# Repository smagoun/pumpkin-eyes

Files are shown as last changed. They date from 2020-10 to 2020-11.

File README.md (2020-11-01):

# pumpkin-eyes
CircuitPython-powered servo control for animatronic eyeballs, inspired by 68percentwater's [arduino servo pumpkin eyes](https://www.youtube.com/watch?v=ryUNHPJ3leY).

Built for Adafruit [ItsyBitsy Express M0](https://www.adafruit.com/product/3727).

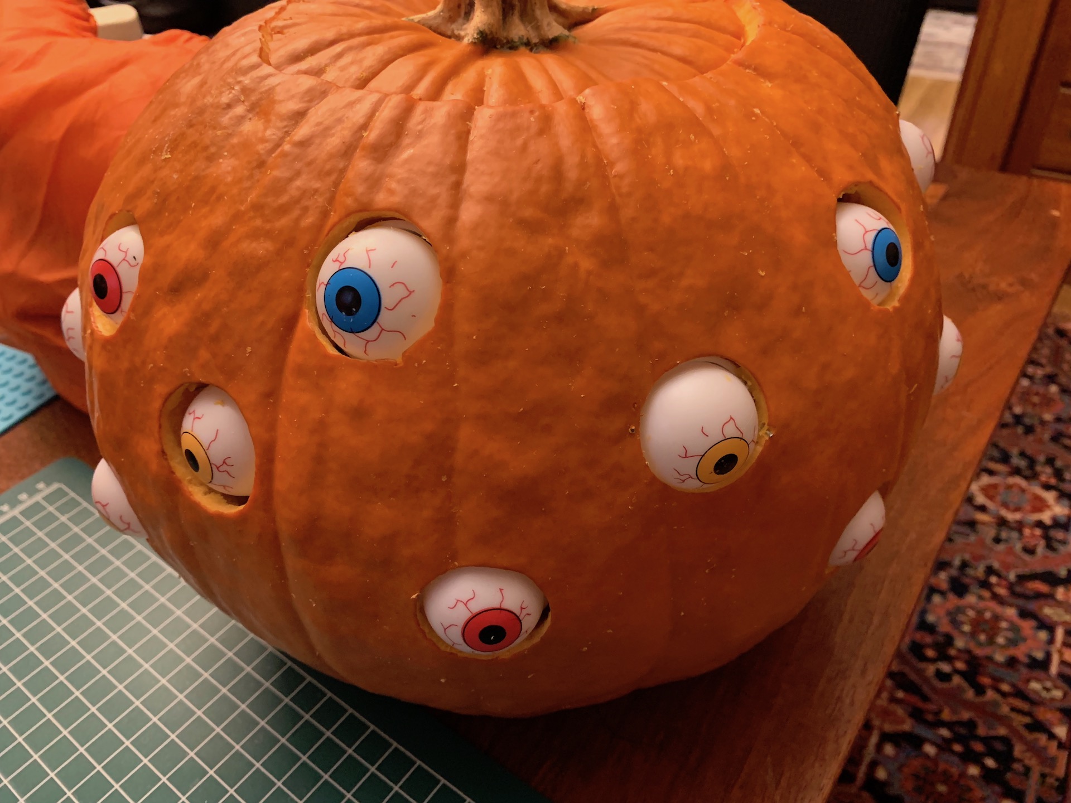
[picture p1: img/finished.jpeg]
Animatronic pumpkin


## Parts list:
* 12x [SG51R Sub-Micro Servos](https://www.adafruit.com/product/2201)
* 1x [ItsyBitsy Express M0](https://www.adafruit.com/product/3727)
* 1x [Half-Size Breadboard](https://www.adafruit.com/product/64)
* 1x [Breadboarding wire bundle](https://www.adafruit.com/product/153)
* 1x [USB Type-A Breakout cable](https://www.adafruit.com/product/4448)
* 1x [NeoPixel Ring - 12x](https://www.adafruit.com/product/1643)
* 1x [Soft tactile button](https://www.adafruit.com/product/3101)
* 2x [1-1/2" sink drain extension tube](https://www.acehardware.com/departments/plumbing/sinks/sink-parts-and-repair/4224051)
* 1x [3-pack of 12 plastic eyeballs](https://www.amazon.com/gp/product/B07582HG6T/ref=ppx_yo_dt_b_asin_title_o03_s00?ie=UTF8&psc=1)
* 1x 5/16" wooden dowel
* Several paper clips, or other stiff wire (baling wire)
* 1x USB battery charger
* 1x large pumpkin (approx 12" diameter)

## Tools:
* Soldering iron
* Wire cutters
* Slip-joint pliers
* Needle-nose pliers
* Hot glue gun
* Fine-tooth razor saw
* File or sandpaper
* Drill with 1/16" and 5/64" bits and 1-3/8" hole saw
* Serrated knife

## Hints + Tips:

### Straightening a paper clip (or baling wire):
1. Pull the paper clip (or wire) mostly-straight by hand
1. If there are bends remaining in the wire, put each bend into the jaws of the pliers and squeeze shut to straighten the bend

### Forming the axles:
1. Straighten a paper clip or other stiff wire and cut a 2" length
1. Use the pliers to bend a short (1/4") 90-degree turn in the wire
1. Feed the other end of the wire through the eyeball (eew!)
1. Bend a 90-degree turn in the other end of the wire, which should now be in a 'U' shape. I found it best to grip the wire with needle-nose pliers just next to the eyeball, then use the slip joint pliers to create the 90-degree bend. Holding the wire with the needle-nose pliers prevents damaging the straight portion of the wire inside the eyeball
1. Use hot glue to affix the bend ends of the wire to the tube. Don't get any glue on the eyeballs!

### Assembling the eyeball mechanism
* Cut the tube into 1" lengths. A little shorter might be better; anything longer will limit the range of motion of the eye.
* The tube I selected happened to fit the eyeballs perfectly. Too perfectly, in fact! Each eyeball has a seam that runs around the middle of the ball. This seam was tall enough to bump into the edge of the tubing. I had to file down the seams on each eyeball to get smooth rotation.
* The eyeballs look better if they have a large range of motion. The range of motion is determined by the relative lengths of the servo horn and the location of the mounting hole in the dowel. To maximize range of motion, mount the control arm close to the base of the dowel. The dowels don't need to be long - 1" is fine.
* For better range of motion, the end of the servo horn should be level with the mounting hole in the dowel. However we also need the mounting hole to be realtively close to the base of the dowel. As a result the servo horn can impact the tube, interfering with range of motion. Cut a notch in the side of the tube to allow the servo horn to traverse freely.
* Use a 5/64" bit to drill the holes in the eyeball. This leaves a little bit of play for the ball to rotate in case the wire isn't perfectly straight.
* Use a 1/16" bit to drill the hole in the dowel for the control arm. This provides a tighter fit for the control arm, and gives better control. A 2" control arm is long enough.

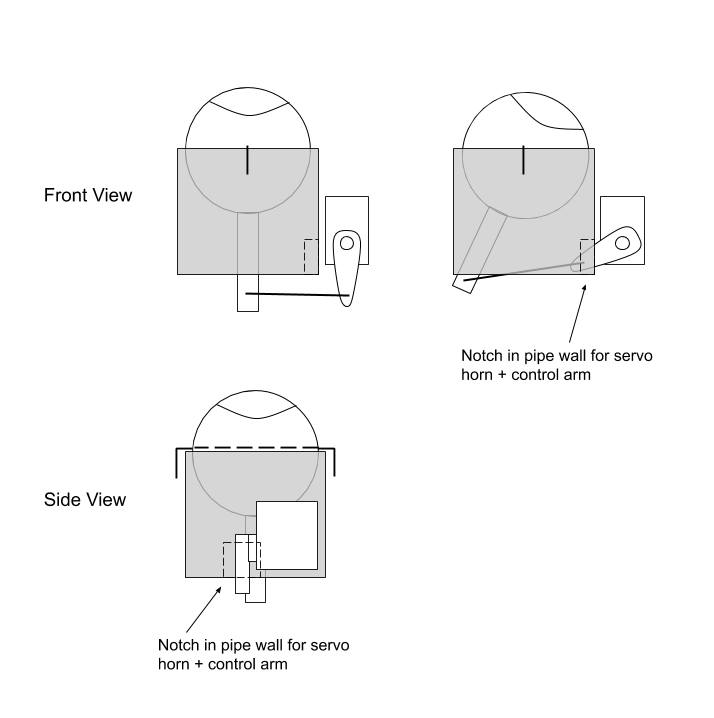
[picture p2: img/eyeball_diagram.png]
Eyeball mechanism diagram


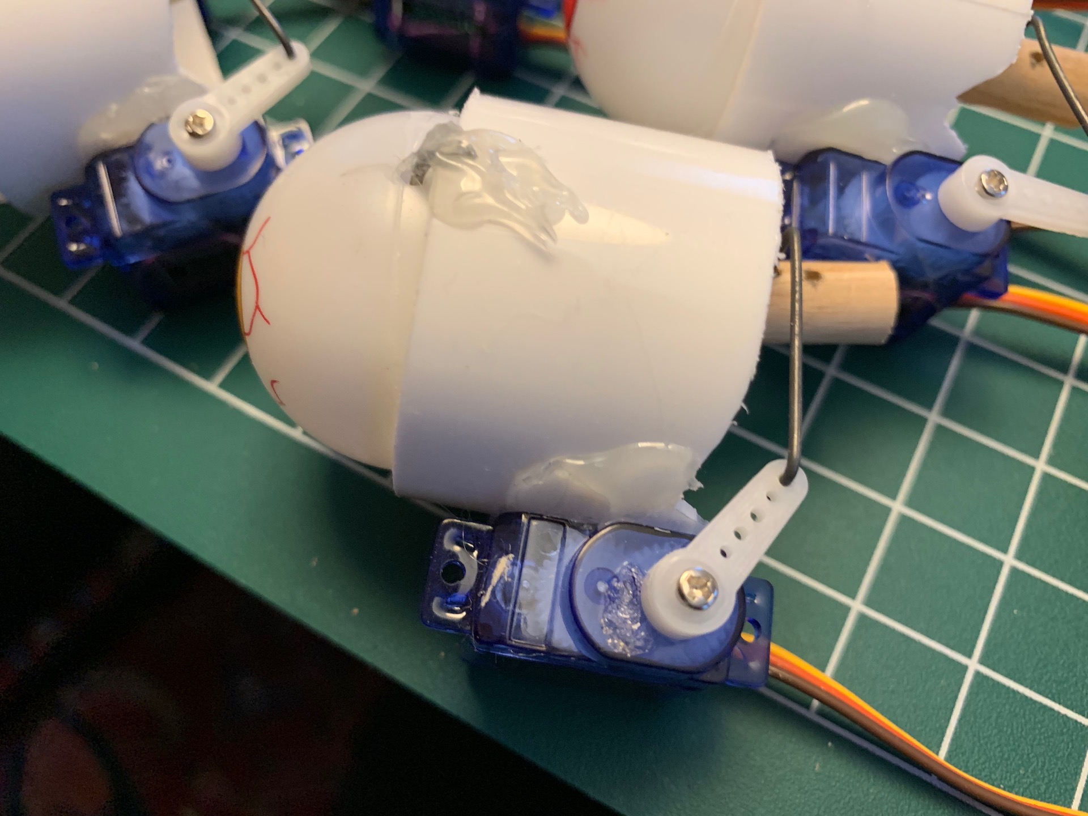
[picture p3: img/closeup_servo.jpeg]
Eyeball closeup


### Notes on the circuit:
* The servos need 4.8v, and many microcontrollers want either 5v or 3.3v. Battery packs often put out 3v, 3.7v, or 6v. Rather than deal with voltage conversion and regulation, I opted for a 5v circuit powered by a USB battery charger. This simplified the wiring, allowing me to use a common 5v rail for both the servos and the microcontroller.
* The ItsyBitsy M0 Express can't power the servos and NeoPixels on its own. Instead, run the battery's power leads to the breadboard's buses. Power each device in parallel off the breadboard's bus.
* Since we're activating servos in batches, power consumption will be very spiky. It might be best to have a capacitor in between the power supply and the power bus, but I didn't look into this. The battery bank didn't seem to mind.
* Though the ItsyBitsy M0 Express is advertised to have 13 PWM outputs, I could only get 11 at one time. To control the 12th servo I piggybacked its control line onto that of another servo.
* The NeoPixels were a late addition. They require a 5v control signal, and have to be powered off the single 5v line (pin 5/D5). This meant piggybacking a second servo onto another's control line in order to free up D5.
* The button in the circuit pauses movement and resets the servos to their midpoint. This was useful to set up the servos for mounting. With the servo horn at the midpoint, I could be confident I was measuring and connecting the control arm properly. The pause button was also useful during debugging.

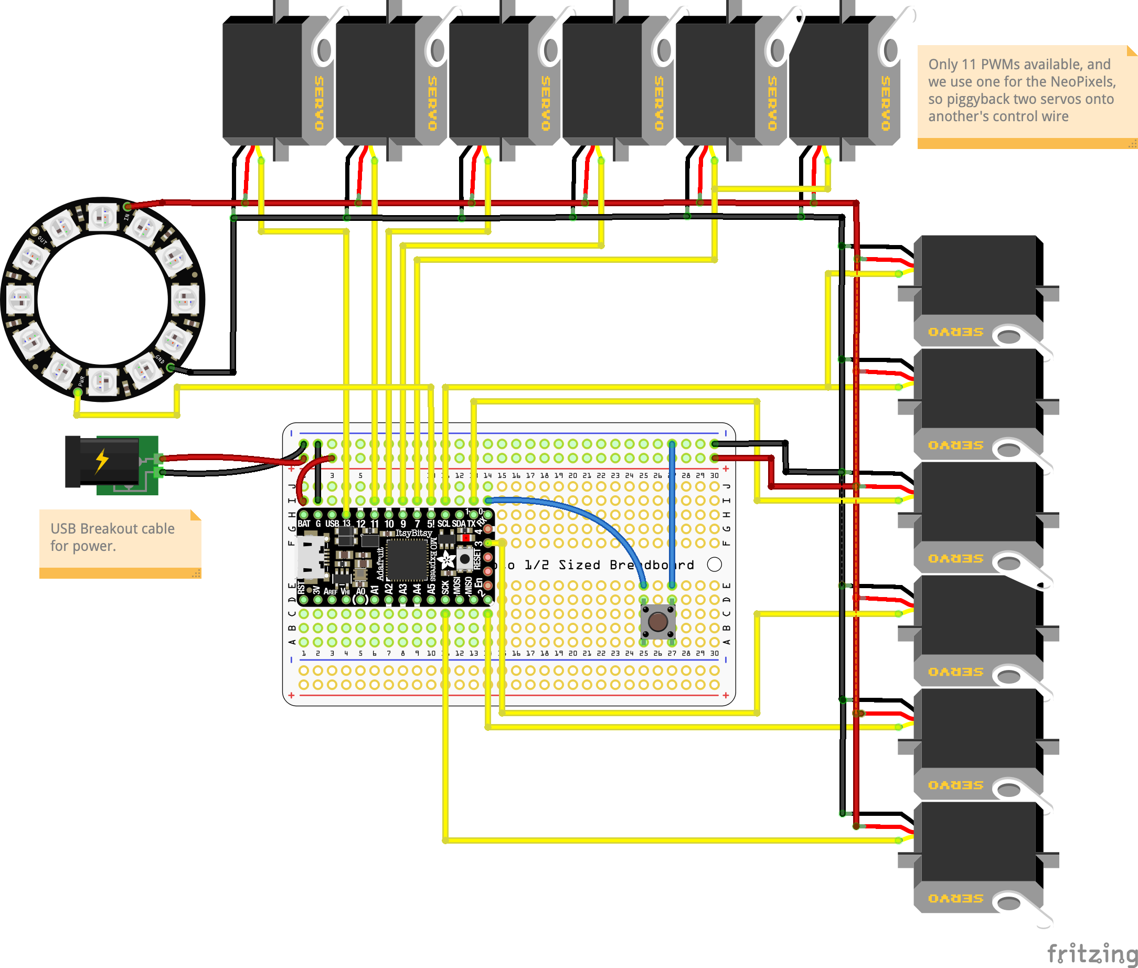
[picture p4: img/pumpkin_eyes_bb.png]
Pumpkin Eyes breadboard


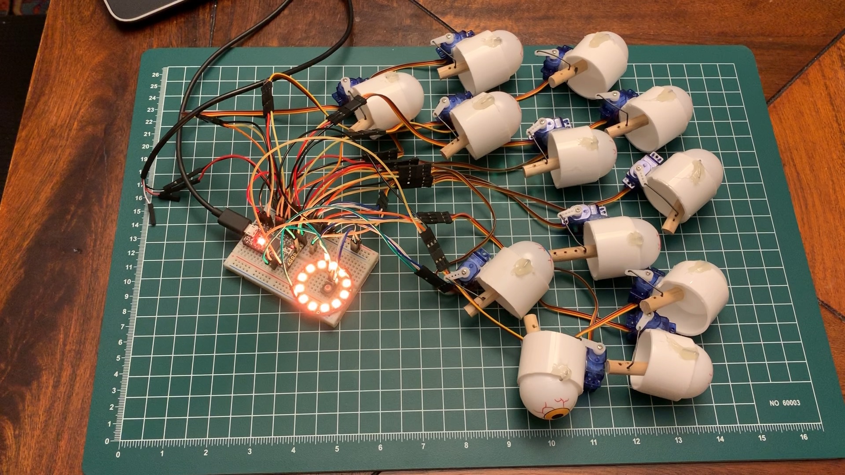
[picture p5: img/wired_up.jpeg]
Wired up


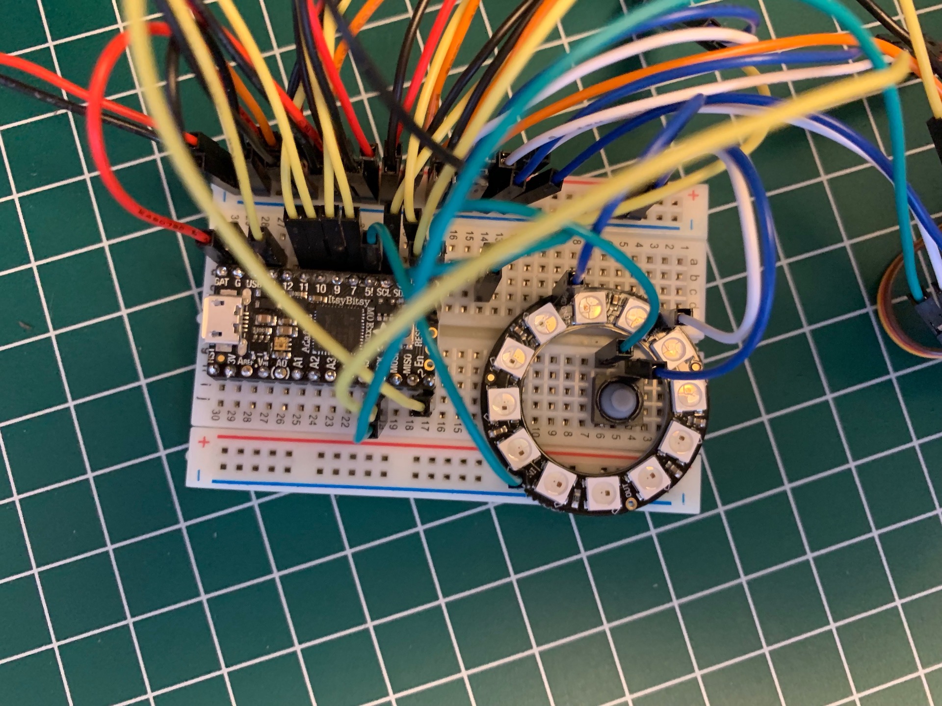
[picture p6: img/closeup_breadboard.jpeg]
Closeup of breadboard


### Installation:
* A larger pumpkin is better; a smaller pumpkin will have much less space to maneuver. 12" diameter was good; 11" might work too.
* Use the hole saw to drill the eye holes. The 1-3/8" saw was perfect for my particular case.
* Enlarge the inside of each hole with a carving knife or similar; carve out some space for each servo, too.
* To get the eyeballs to stay in the pumpkin, I hot-glued a pair of 1" wires (from a paper clip) to each tube. These stuck into the flesh of the pumpkin and kept the eyeball assemblies in place. Mostly.
* I installed each eyeball assembly separately, then plugged them all in at the end. Use a bit of tape to hold keep each servo's wiring together.
* Cut a hole in the bottom rear of the pumpkin to run the USB power lead out to a battery. This keeps the battery outside and free of pumpkin goop.

## Notes for next time:
* The breadboard-and-jumper-wire setup is quite fragile; wires will pop out without much provocation. For reuse this needs a more-durable wiring harness.
* Carving the pumpkin takes longer than expected - set aside a couple hours.
* Find a better way to secure the eyeball mechanism to the inside of the pumpkin.
* Consider reducing the delay between eye movement to make it "twitchier"
* Try a whiter (less red) flame
* It's best viewed in daylight!

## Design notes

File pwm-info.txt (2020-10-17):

# PWM available on the following, though not all at once!

# From https://learn.adafruit.com/introducing-itsy-bitsy-m0/circuitpython-pwm:

No PWM on: A0
No PWM on: A1
PWM on: A2
PWM on: A3
PWM on: A4
No PWM on: A5
PWM on: APA102_MOSI
PWM on: APA102_SCK
PWM on: D0
PWM on: D1
PWM on: D10
PWM on: D11
PWM on: D12
PWM on: D13
PWM on: D2
PWM on: D3
PWM on: D4
PWM on: D5
PWM on: D6
PWM on: D7
PWM on: D8
PWM on: D9
PWM on: L
PWM on: MISO
PWM on: MOSI
PWM on: RX
PWM on: SCK
PWM on: SCL
PWM on: SDA
PWM on: TX

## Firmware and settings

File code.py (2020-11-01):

# Control code for creepy pumpkin eyes.
#
# Based on Adafruit Itsy Bitsy M0 Express IO demo

import board
import time
import gc
import random
from digitalio import DigitalInOut, Direction, Pull
import pulseio
import adafruit_dotstar
from adafruit_motor import servo
import neopixel

FREQ=50
ANGLE_MIN=0
ANGLE_MAX=180
ANGLE_MIDPOINT=90

# One pixel connected internally!
dot = adafruit_dotstar.DotStar(board.APA102_SCK, board.APA102_MOSI, 1, brightness=0.5)

# Neopixel ring
pixel_pin = board.D5
num_pixels = 12
pixels = neopixel.NeoPixel(pixel_pin, num_pixels, brightness=0.3, auto_write=False)

# Built in red LED. Conflicts with servo on D13 below
# led = DigitalInOut(board.D13)
# led.direction = Direction.OUTPUT

# Global state
running = True
staring = False

# Button to toggle between run and standby (servos back to midpoint)
button = DigitalInOut(board.D0)
button.direction = Direction.INPUT
button.pull = Pull.UP

# Pin numbers and ordering figured out by a bit of trial and error
servo1 = servo.Servo(pulseio.PWMOut(board.D10, frequency=FREQ))
servo2 = servo.Servo(pulseio.PWMOut(board.D1, frequency=FREQ))
servo3 = servo.Servo(pulseio.PWMOut(board.D2, frequency=FREQ))
servo4 = servo.Servo(pulseio.PWMOut(board.D3, frequency=FREQ))
# NeoPixels need a 5V logic line, so piggyback servo 5 onto some other servo's pin
# so we can free up D5
# servo5 = servo.Servo(pulseio.PWMOut(board.D5, frequency=FREQ))
servo6 = servo.Servo(pulseio.PWMOut(board.D7, frequency=FREQ))
servo7 = servo.Servo(pulseio.PWMOut(board.D9, frequency=FREQ))
servo8 = servo.Servo(pulseio.PWMOut(board.D11, frequency=FREQ))
servo9 = servo.Servo(pulseio.PWMOut(board.D13, frequency=FREQ))   # Side effect, controls LED
servo10 = servo.Servo(pulseio.PWMOut(board.SCK, frequency=FREQ))
servo11 = servo.Servo(pulseio.PWMOut(board.SCL, frequency=FREQ))
# Can't figure out how to get a 12th PWM, so piggyback servo 12 on some other servo's pin
# servo12 = servo.Servo(pulseio.PWMOut(board.A2, frequency=FREQ))


######################### HELPERS ##############################

def randomOrange():
    '''Generate a random orange-ish color, like a flame'''
    r = random.randint(200, 255)
    g = random.randint(0, 60)
    r = r if r > g else g
    b = 0
    return [r, g, b]

def flicker(dot, pixels):
    '''Change color + brightness. Assumes a single DotStar and a set of NeoPixels'''
    brightness = random.random()
    orange = randomOrange()

    dot[0] = orange
    dot.brightness = brightness

    pixels.fill(orange)
    pixels.brightness = brightness
    pixels.show()

def checkButton():
    '''Toggle the 'running' global on button press'''
    if (not button.value):  # Button pressed
        global running
        running = not running
    while (not button.value):    # Wait for button to be released
        time.sleep(0.1)


def lookAround():
    '''Main routine to look all around'''
    # Group 1
    servo1.angle = random.randint(ANGLE_MIN, ANGLE_MAX)
    servo2.angle = random.randint(ANGLE_MIN, ANGLE_MAX)
    servo3.angle = random.randint(ANGLE_MIN, ANGLE_MAX)
    servo4.angle = random.randint(ANGLE_MIN, ANGLE_MAX)

    for i in range(random.randint(0, 4)):
        flicker(dot, pixels)
        time.sleep(0.1)
        checkButton()


    # Group 2
    # servo5 needs to be piggybacked on some other servo's pin - see above
    # servo5.angle = random.randint(ANGLE_MIN, ANGLE_MAX)
    servo6.angle = random.randint(ANGLE_MIN, ANGLE_MAX)
    servo7.angle = random.randint(ANGLE_MIN, ANGLE_MAX)
    servo8.angle = random.randint(ANGLE_MIN, ANGLE_MAX)

    for i in range(random.randint(0, 4)):
        flicker(dot, pixels)
        time.sleep(0.1)
        checkButton()

    # Group 3
    servo9.angle = random.randint(ANGLE_MIN, ANGLE_MAX)
    servo10.angle = random.randint(ANGLE_MIN, ANGLE_MAX)
    servo11.angle = random.randint(ANGLE_MIN, ANGLE_MAX)
    # servo12 needs to be piggybacked on some other servo's pin - see above
    # servo12.angle = random.randint(ANGLE_MIN, ANGLE_MAX)

    for i in range(random.randint(0, 4)):
        flicker(dot, pixels)
        time.sleep(0.1)
        checkButton()


def stare():
    '''Reset servos to midpoint'''
    global staring
    if (not staring):
        servo1.angle = ANGLE_MIDPOINT
        servo2.angle = ANGLE_MIDPOINT
        servo3.angle = ANGLE_MIDPOINT
        servo4.angle = ANGLE_MIDPOINT
        # servo5 needs to be piggybacked on some other servo's pin - see above
        # servo5.angle = ANGLE_MIDPOINT
        servo6.angle = ANGLE_MIDPOINT
        servo7.angle = ANGLE_MIDPOINT
        servo8.angle = ANGLE_MIDPOINT
        servo9.angle = ANGLE_MIDPOINT
        servo10.angle = ANGLE_MIDPOINT
        servo11.angle = ANGLE_MIDPOINT
        # servo12 needs to be piggybacked on some other servo's pin - see above
        # servo12.angle = ANGLE_MIDPOINT
        staring = True


######################### MAIN LOOP ##############################

while True:
    checkButton()   # No interrupts in CircuitPython, so we have to poll
    if running:
        staring = False
        lookAround()
    else:
        stare()

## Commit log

2020-10-17 Initial code for pumpkin eyeball controller
2020-10-17 Add support for a button on D0 that pauses the servos and resets them to the midpoint.
    [code.py]
2020-10-20 Add Fritzing breadboard/schematic
    Requires installing "Itsy Bitsy M0 Express.fzpz" from the Adafruit Fritzing Library: https://github.com/adafruit/Fritzing-Library.
    [pumpkin_eyes.fzz]
2020-11-01 Update schematic for addition of NeoPixel ring
    [pumpkin_eyes.fzz]
